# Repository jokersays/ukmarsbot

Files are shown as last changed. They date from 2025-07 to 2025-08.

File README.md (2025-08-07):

# update CW2025
## wall sensor
- LED (sichtbares Licht): TCLR5800 https://eu.mouser.com/ProductDetail/Vishay-Semiconductors/TLCR5800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
- Phototransistor: BPW96B https://www.mouser.de/ProductDetail/Vishay-Semiconductors/BPW96B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

## motor
- N20 Gear Motor mit Encoder, 6V, 20:1 / ~1000 RPM (oder 750 RPM) AliExpress?

## capacitor
- 470uF 10V 6.3mm, <12mm h, radial 2.5
- 330uF 10V radial 2.5
--> mouser

# ukmarsbot

__A simple beginner's multi purpose robot platform__

Using inexpensive, readily available materials, components and techniques, the UK Micromouse and Robotics Society (UKMARS) has created a basic robot design that can be used in a variety of common contests such as line following, wall following, drag race and mini-sumo.

UKMARSBOT V1.0 with basic wall sensor

## Contents

This repository is all about the robot itself. Software is provided in other UKMARS repositories. 

 - Software examples https://github.com/ukmars/ukmarsbot-examples
 - Full maze solving software: https://github.com/ukmars/ukmarsbot-mazerunner

The repository has a number of sections:

 - [__docs__](docs) contains miscellaneous documentation and datasheets. In there are some notes about design decisions and constraints, processor choice and configuration, and a bit about sensors.
 - [__ecad__](ecad) contains the design files for the various electronic modules that make up the robot. The original development was done with Eagle Version 7 since it was the last 'free' version of Eagle. More recent versions are likely to be developed in KiCad since it is free, unconstrained and multiplatform. You are only likely to need to look in here f you want to modify existing modules or create your own. Either Eagle or KiCad can be used for new development.
 - [__hardware__](hardware) holds subsections for the major parts that make up the robot - the main PCB and all the sensor boards. This is where you find the outputs from the ECAD tools. You don't need to know anything about Eagle or KiCad to use these outputs. For each module you should find a set of gerbers in a zip file so that you can easily order boards from your favourite supplier. Also present should be the schematics in PDF form, images of the finished boards and a parts list (BOM) to help you populate the board and select components. Note that many component choices are up to the builder and there are a number of options possible. Some or all of these elements may be missing or incomplete. Let us know of any shortcomings by raising [a new issue on github](https://github.com/ukmars/ukmarsbot/issues).
 - [__mechanical__](mechanical) contains a number of mechanical CAD files. These are most likely to be STL or STEP files  and are for components that can be 3D printed tohelp you make your robot. For example you will find motor mounts and brackets here.
 - [__renders__](renders) is a place where we keep generated images of the robot and some components. You can get an idea of how your finished robot may look as well as see some of the prototypes that led to the current design.
 - [__resources__](resources) is really a dump for stuff that does not fit in with the rest. At the tie of writing this is just a section about data logging.

## The Processor
Processor power is provided by the Arduino Nano board because it is very cheap and widely available. There is a huge range of sample code available for almost any purpose and support is easily found online. The Arduino software can be installed on any computer and is free.

A proposed pin usage for an Arduino Nano controller can be found in the [docs](docs) folder.

because the Arduino Nano is a popular processor module, there are many compatible or near-compatible alternative boards available. The processor module socket makes it possible to use some of these directly with only small modifications or, with a little more work you might fit almost any processor. Variants have already been built with STM32 processors and even a Raspberry Pi pico and Zero board.

## Bluetooth

Some alternative processors in the Arduino range already have Bluetooth and WiFi built in. If you stick with simpler options - like the Arduino Nano - there is a connector provided for you to attach one of the common HC05 or HC06 Bluetooth modules directly to the board to make a wireless serial connection. Circuitry on the board (V1.1 and later) allowyou to leave the BT module connected during programming. You can then use any serial terminal, including the Arduino terminal, to communicate with the robot over Bluetooth.

### Coding
The easiest language for starting coding with the Arduino, and the method most people use, is to create a  "Sketch" using the Arduino Integrated Development Environment (IDE). A "Sketch" comprises functions written with C/C++ statements and the Arduino IDE takes care of turning the sketch into a complete program and uploading it to the Arduino board. It can run on any of the major platforms: Windows, Mac and Linux enabling Sketch programs for the Arduino to be readily developed on any PC. The Arduino project has lots of examples and help available for creating code, as well as libraries of functions to carry out specific tasks.

The Arduino IDE requires software to be downloaded and installed on the development PC as well as drivers to enable the developed code to be downloaded using the USB cable onto the Arduino board. All of this software and drivers are free and easy to install as long as you have software install permissions on the PC.

There is also a recently introduced web based development environment, but as yet this does not support all Arduino models and platforms. and still requires various plug ins to be installed on the development PC to use it. Find out more here: https://www.arduino.cc/en/software

A very popular alternative to the Arduino IDE is PlatformIO which can be fully integrated into the excellent VSCode editor. A 'getting started' guide for this environment is available here: https://docs.platformio.org/en/latest/integration/ide/vscode.html

Alternative software environments are available and are identified at the end of this document.

### Hardware

The robot hardware is constrained by the various contest events to be within certain dimensional limits. That means that the basic chassis will be smaller than 100mm x 100mm although add-on sensors for individual events will increase the size. The robot is designed to be multipurpose so there is a core hardware setup that provides for a basic wheelchair drive of two motors, encoder feedback for individual motor speed and a minimal interface for user interaction. Components will be modular so that substitutions are easy and to provide the greatest flexibility. Builders are free to make whatever modifications suit their purpose. For example, larger or smaller motors and wheels may be used and a variety of sensor options are possible.

### Power Supply

For most purposes, the power supply for the robot will need to be compact, readily available and easy to recharge. Non rechargeable batteries are not economically viable for robot experiment and are, in any case, less environmentally friendly. Safety is a concern and so Lithium Polymer cells are only recommended when part of a regulated and protected pack. Perhaps the most common small battery is the rechargeable PP3 sized pack running at 8.4 Volts or 9 Volts. Rechargeable cells and their chargers can be purchased at supermarkets and online suppliers. More confident, or adventurous builders may install whatever power supply suits them.

### Motors

While there is endless variety in small DC electric motors, the N20-based gearmotors are excellent value for money and can be purchased in a huge range of performance characteristics. An example can be found here: [Pimoroni 20:1 gearmotor](https://shop.pimoroni.com/products/micro-metal-gearmotor-extended-back-shaft?variant=32587847050). The common dimensions make it easy to swap motors without changing the mechanical design of the robot. Versions are available with built-in encoders allowing for more accurate control of speed and greater precision in movement of the robot. Normally these would be used in any robot. The drivers for these motors are available on small circuit board modules that can easily be connected with the Arduino Nano.

### Materials

It will be possible to build the robot using parts that are commercially readily available and specialist materials will not be required. Access to basic hand tools and soldering equipment will be necessary.

It is likely that some builders will have some access to a 3D printer or a laser cutter or both and the open design of the robot with upgrade paths will allow advanced builders to utilize these tools to create higher performing robots.

### Software

The two software repositories mentioned above provide a fairly complete set of examples and code for almost every aspect of programming for the UKMARSBOT platform. Many of the techniques and examples will also be directly applicable to other mobile robot projects.

If the Arduino IDE is not for you, then there are other programming choices to suit you. (__None of these have been tried by UKMARS__)

* FlashForth http://flashforth.com/ is a Forth stamp system implemented on the Microchip 8-bit PIC18F and 16-bit PIC24, 30, 33 and the Atmel Atmega microcontroller families. See also https://playground.arduino.cc/CommonTopics/ForthOnArduino/ for other options relating to Forth.

* For Basic users there appear to be fewer options. One of these is Great Cow basic http://gcbasic.sourceforge.net/Typesetter/index.php/Home. _"The  Great Cow BASIC suite is robust and fully functional compiler and assembler.   Using Great Cow BASIC is the fastest method to program a Microchip PIC or Atmel AVR 8-bit microcontroller for those just starting and the professional user."_  The host software is cross platform and there is a graphical editor as well as a more traditional IDE.

* Some users may prefer a visual programming environment similar to Scratch. Several of these are available and more information may be found here [Sparkfun Alternative Arduino Interfaces](https://learn.sparkfun.com/tutorials/alternative-arduino-interfaces/all).

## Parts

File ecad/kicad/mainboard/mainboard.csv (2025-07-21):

'Reference' | 'Value' | 'Footprint' | 'Datasheet' | 'Qty' | 'DNP' | 'Exclude from BOM' | 'Exclude from Board'
'C1' | '100n' | 'ukmarsbot:C_Rect_L4.6mm_W2.0mm_P2.50mm_MKS02_FKP02' | '~' | '1' | '' | '' | ''
'C2,C3' | '330uF, 16V' | 'Capacitor_THT:CP_Radial_D8.0mm_P2.50mm' | '~' | '2' | '' | '' | ''
'D1' | '1N5401' | 'Diode_THT:D_DO-201AD_P15.24mm_Horizontal' | '~' | '1' | '' | '' | ''
'D3' | '1N4148' | 'Diode_THT:D_DO-35_SOD27_P7.62mm_Horizontal' | 'https://assets.nexperia.com/documents/data-sheet/1N4148_1N4448.pdf' | '1' | '' | '' | ''
'H1,H2,H3,H4,H5,H6' | 'MountingHole' | 'ukmarsbot:MountingHole_3.2mm_M3_clearance' | '~' | '6' | '' | '' | ''
'IC1' | '74HC86' | 'Package_DIP:DIP-14_W7.62mm_LongPads' | 'http://www.ti.com/lit/gpn/sn74HC86' | '1' | '' | '' | ''
'J1' | 'SENSORS' | 'ukmarsbot:1X14_LOCK_LONGPADS' | '' | '1' | '' | '' | ''
'J2,J3' | 'CONN_06SILK_FEMALE_PTH' | 'ukmarsbot:1X06_LOCK_LONGPADS' | '' | '2' | '' | '' | ''
'J4' | 'POWER' | 'Connector_Molex:Molex_KK-254_AE-6410-02A_1x02_P2.54mm_Vertical' | '~' | '1' | '' | '' | ''
'J5' | 'SERIAL' | 'ukmarsbot:1X04_LOCK_LONGPADS' | '' | '1' | '' | '' | ''
'M1' | 'Left Motor' | 'ukmarsbot:MINI-METAL-GEARMOTOR-WITH-BRACKET' | '~' | '1' | '' | '' | ''
'M2' | 'Right Motor' | 'ukmarsbot:MINI-METAL-GEARMOTOR-WITH-BRACKET' | '~' | '1' | '' | '' | ''
'R1,R2,R10' | '10k' | 'ukmarsbot:R_Axial_DIN0207_L6.3mm_D2.5mm_P7.62mm_BIGPAD' | '~' | '3' | '' | '' | ''
'R3,R11' | '4k7' | 'ukmarsbot:R_Axial_DIN0207_L6.3mm_D2.5mm_P7.62mm_BIGPAD' | '~' | '2' | '' | '' | ''
'R4' | '2k2' | 'ukmarsbot:R_Axial_DIN0207_L6.3mm_D2.5mm_P7.62mm_BIGPAD' | '~' | '1' | '' | '' | ''
'R5' | '1k0' | 'ukmarsbot:R_Axial_DIN0207_L6.3mm_D2.5mm_P7.62mm_BIGPAD' | '~' | '1' | '' | '' | ''
'R6' | '470' | 'ukmarsbot:R_Axial_DIN0207_L6.3mm_D2.5mm_P7.62mm_BIGPAD' | '~' | '1' | '' | '' | ''
'R7,R8' | '15k' | 'ukmarsbot:R_Axial_DIN0207_L6.3mm_D2.5mm_P7.62mm_BIGPAD' | '~' | '2' | '' | '' | ''
'S1' | 'sub-miniature, SPDT' | 'ukmarsbot:SW_MINI-SPDT-RTECH-78-0564' | 'https://static.rapidonline.com/pdf/560602t_v1.pdf' | '1' | '' | '' | ''
'S2' | 'BUTTON' | 'ukmarsbot:TACTILE_SWITCH_PTH_6.0MM' | '' | '1' | '' | '' | ''
'S3' | 'DIP-SW' | 'ukmarsbot:SW_DIP_SPSTx04_Slide_6.7x11.72mm_W7.62mm_P2.54mm_LowProfile' | '' | '1' | '' | '' | ''
'U1' | 'Arduino_Nano' | 'ukmarsbot:Arduino_Nano' | 'https://store.arduino.cc/usa/arduino-nano' | '1' | '' | '' | ''
'U2' | 'TB6612FNG-Module' | 'ukmarsbot:TB6612FNG-module' | 'https://cdn.shopify.com/s/files/1/0174/1800/files/TB6612FNG_3e2152f9-ac47-436b-bb2d-0abf1ce342e0.pdf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' | '1' | '' | '' | ''

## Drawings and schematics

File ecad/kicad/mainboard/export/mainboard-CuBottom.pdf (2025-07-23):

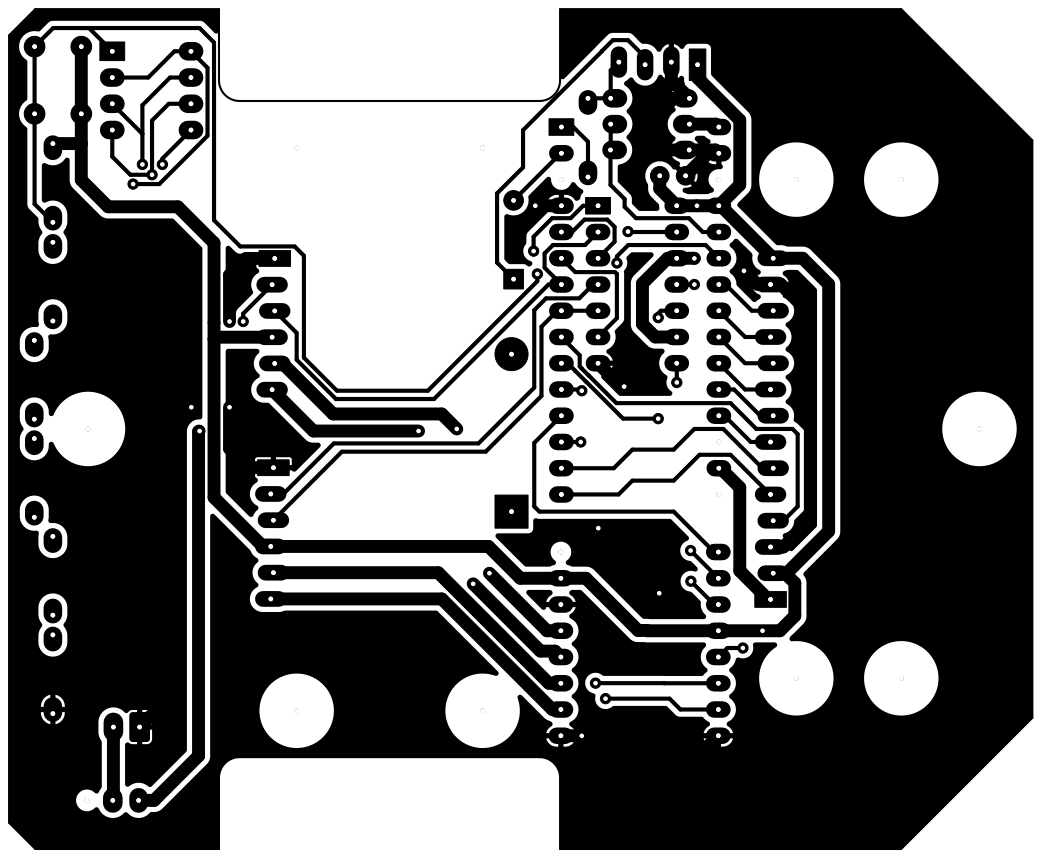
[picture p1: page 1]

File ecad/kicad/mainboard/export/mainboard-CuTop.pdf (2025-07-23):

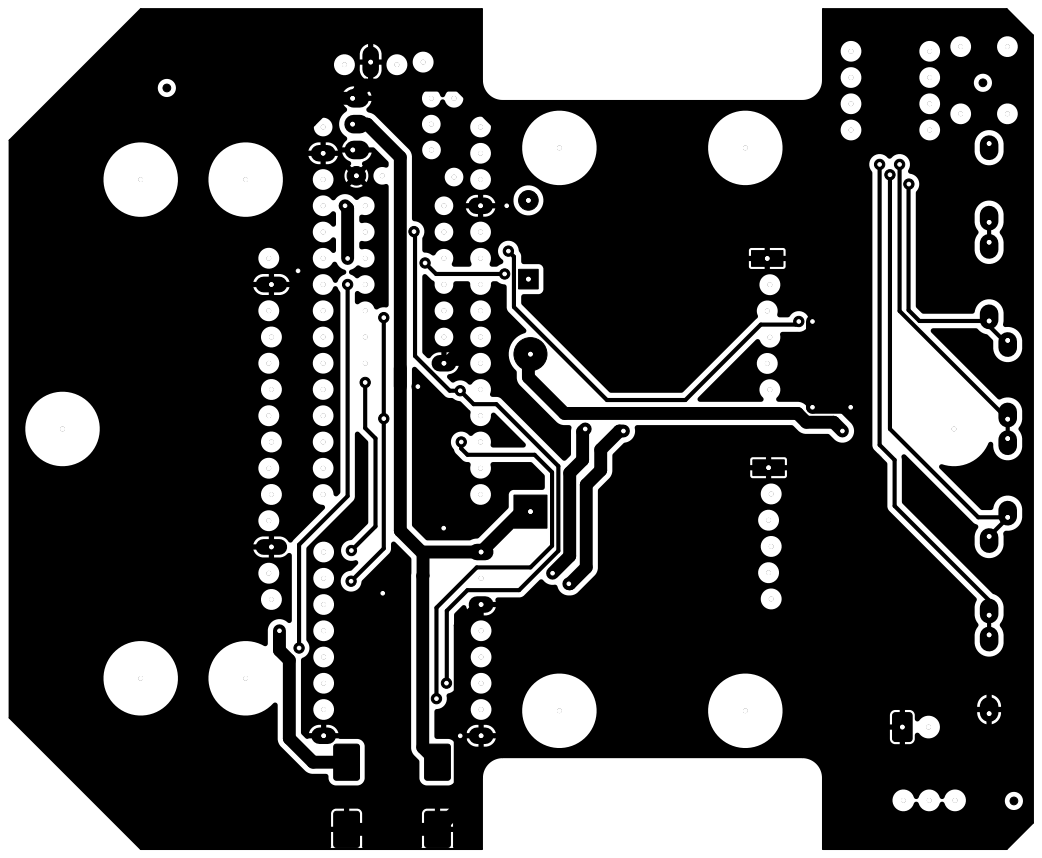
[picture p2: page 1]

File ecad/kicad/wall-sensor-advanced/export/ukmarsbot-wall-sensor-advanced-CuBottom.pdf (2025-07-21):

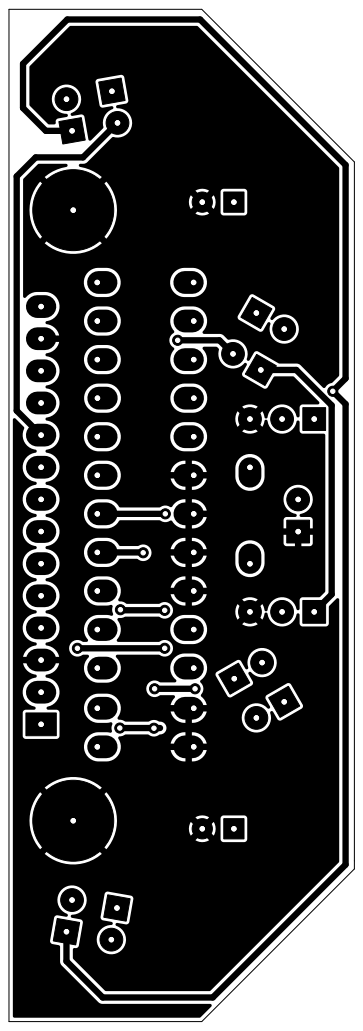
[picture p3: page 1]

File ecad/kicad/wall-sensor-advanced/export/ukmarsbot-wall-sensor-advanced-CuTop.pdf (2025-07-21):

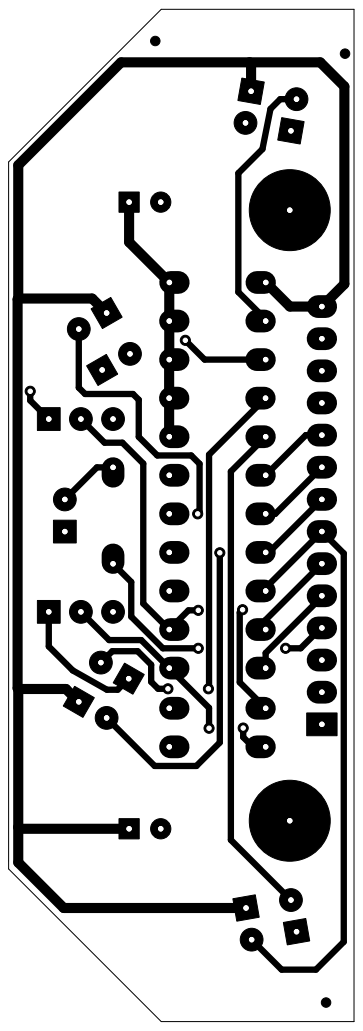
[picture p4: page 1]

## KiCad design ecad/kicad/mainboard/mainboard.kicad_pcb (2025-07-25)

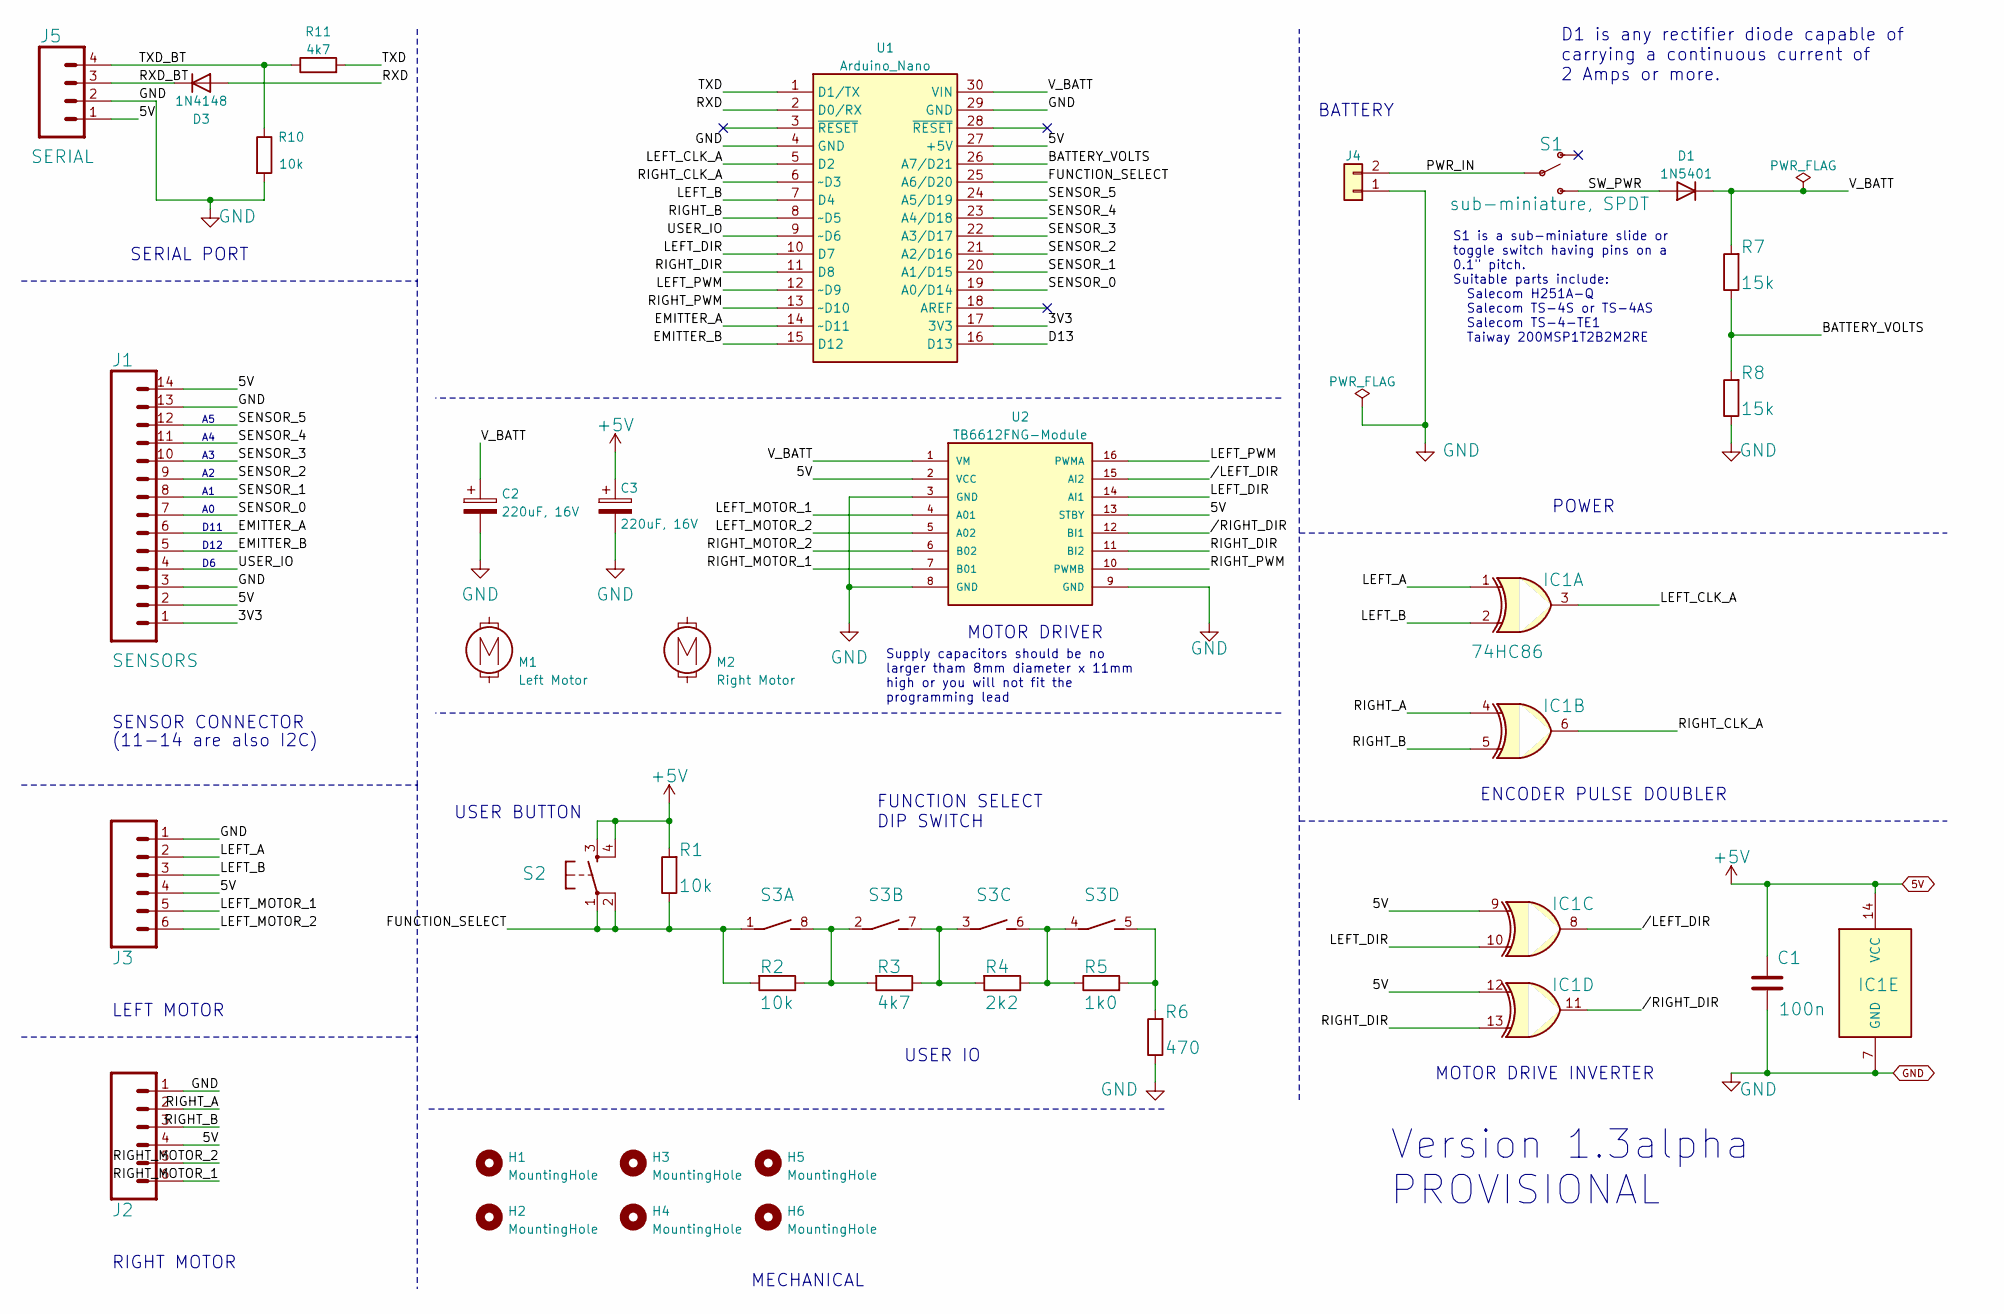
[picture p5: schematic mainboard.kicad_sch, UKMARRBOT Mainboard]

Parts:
C1: 100n; C_Rect_L4.6mm_W2.0mm_P2.50mm_MKS02_FKP02
C2, C3: 220uF, 16V; CP_Elec_8x10
D1: 1N5401; D_DO-201AD_P15.24mm_Horizontal
D3: 1N4148; D_DO-35_SOD27_P7.62mm_Horizontal
H1, H2, H3, H4, H5, H6: MountingHole; MountingHole_3.2mm_M3_clearance
IC1: 74HC86; DIP-14_W7.62mm_LongPads
J1: SENSORS; 1X14_LOCK_LONGPADS
J2, J3: CONN_06SILK_FEMALE_PTH; 1X06_LOCK_LONGPADS
J4: POWER; Molex_KK-254_AE-6410-02A_1x02_P2.54mm_Vertical
J5: SERIAL; 1X04_LOCK_LONGPADS
M1: Left Motor; MINI-METAL-GEARMOTOR-WITH-BRACKET
M2: Right Motor; MINI-METAL-GEARMOTOR-WITH-BRACKET
R1, R2, R10: 10k; R_Axial_DIN0207_L6.3mm_D2.5mm_P7.62mm_BIGPAD
R3, R11: 4k7; R_Axial_DIN0207_L6.3mm_D2.5mm_P7.62mm_BIGPAD
R4: 2k2; R_Axial_DIN0207_L6.3mm_D2.5mm_P7.62mm_BIGPAD
R5: 1k0; R_Axial_DIN0207_L6.3mm_D2.5mm_P7.62mm_BIGPAD
R6: 470; R_Axial_DIN0207_L6.3mm_D2.5mm_P7.62mm_BIGPAD
R7, R8: 15k; R_Axial_DIN0207_L6.3mm_D2.5mm_P7.62mm_BIGPAD
S1: sub-miniature, SPDT; SW_MINI-SPDT-SW
S2: BUTTON; TACTILE_SWITCH_PTH_6.0MM
S3: DIP-SW; SW_DIP_SPSTx04_Slide_6.7x11.72mm_W7.62mm_P2.54mm_LowProfile
U1: Arduino_Nano
U2: TB6612FNG-Module; TB6612FNG-module; PARTREV 11-13-17

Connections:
5V: C1.1, C3.1, IC1.9, IC1.12, IC1.14 (VCC), J1.2, J1.14, J2.4, J3.4, J5.1, R1.2, S2.3, S2.4, U1.27 (+5V), U2.2 (VCC), U2.13 (STBY)
/3V3: J1.1, U1.17 (3V3)
/BATTERY_VOLTS: R7.1, R8.2, U1.26 (A7/D21)
/D13: U1.16 (D13)
/EMITTER_A: J1.6, U1.14 (~D11)
/EMITTER_B: J1.5, U1.15 (D12)
/FUNCTION_SELECT: R1.1, R2.2, S2.1, S2.2, S3.1, U1.25 (A6/D20)
/LEFT_A: IC1.1, J3.2
/LEFT_B: IC1.2, J3.3, U1.7 (D4)
/LEFT_CLK_A: IC1.3, U1.5 (D2)
/LEFT_DIR: IC1.10, U1.10 (D7), U2.14 (AI1)
/LEFT_MOTOR_1: J3.5, U2.4 (A01)
/LEFT_MOTOR_2: J3.6, U2.5 (A02)
/LEFT_PWM: U1.12 (~D9), U2.16 (PWMA)
/PWR_IN: J4.2, S1.2
/RIGHT_A: IC1.4, J2.2
/RIGHT_B: IC1.5, J2.3, U1.8 (~D5)
/RIGHT_CLK_A: IC1.6, U1.6 (~D3)
/RIGHT_DIR: IC1.13, U1.11 (D8), U2.11 (BI2)
/RIGHT_MOTOR_1: J2.6, U2.7 (B01)
/RIGHT_MOTOR_2: J2.5, U2.6 (B02)
/RIGHT_PWM: U1.13 (~D10), U2.10 (PWMB)
/RXD: D3.2 (A), U1.2 (D0/RX)
/RXD_BT: D3.1 (K), J5.3
/SENSOR_0: J1.7, U1.19 (A0/D14)
/SENSOR_1: J1.8, U1.20 (A1/D15)
/SENSOR_2: J1.9, U1.21 (A2/D16)
/SENSOR_3: J1.10, U1.22 (A3/D17)
/SENSOR_4: J1.11, U1.23 (A4/D18)
/SENSOR_5: J1.12, U1.24 (A5/D19)
/SW_PWR: D1.2 (A), S1.3 (S)
/TXD: R11.2, U1.1 (D1/TX)
/TXD_BT: J5.4, R10.1, R11.1
/USER_IO: J1.4, U1.9 (~D6)
/V_BATT: C2.1, D1.1 (K), R7.2, U1.30 (VIN), U2.1 (VM)
//LEFT_DIR: IC1.8, U2.15 (AI2)
//RIGHT_DIR: IC1.11, U2.12 (BI1)
GND: C1.2, C2.2, C3.2, IC1.7 (GND), J1.3, J1.13, J2.1, J3.1, J4.1, J5.2, R6.1, R8.1, R10.2, U1.4 (GND), U1.29 (GND), U2.3 (GND), U2.8 (GND), U2.9 (GND)
unnamed: R2.1, R3.2, S3.2 (1), S3.8 (2)
unnamed: R3.1, R4.2, S3.3 (1), S3.7 (2)
unnamed: R4.1, R5.1, S3.4 (1), S3.6 (2)
unnamed: R5.2, R6.2, S3.5 (2)

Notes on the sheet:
MOTOR DRIVER
D1 is any rectifier diode capable of carrying a continuous current of 2 Amps or more.
USER IO
POWER
MOTOR DRIVE INVERTER
FUNCTION SELECT DIP SWITCH
Supply capacitors should be no larger tham 8mm diameter x 11mm high or you will not fit the programming lead
S1 is a sub-miniature slide or toggle switch having pins on a 0.1" pitch. Suitable parts include: Salecom H251A-Q Salecom TS-4S or TS-4AS Salecom TS-4-TE1 Taiway 200MSP1T2B2M2RE
RIGHT MOTOR
SERIAL PORT
SENSOR CONNECTOR
BATTERY
MECHANICAL
ENCODER PULSE DOUBLER
USER BUTTON
D11
Version 1.3alpha PROVISIONAL
LEFT MOTOR
(11-14 are also I2C)
D12

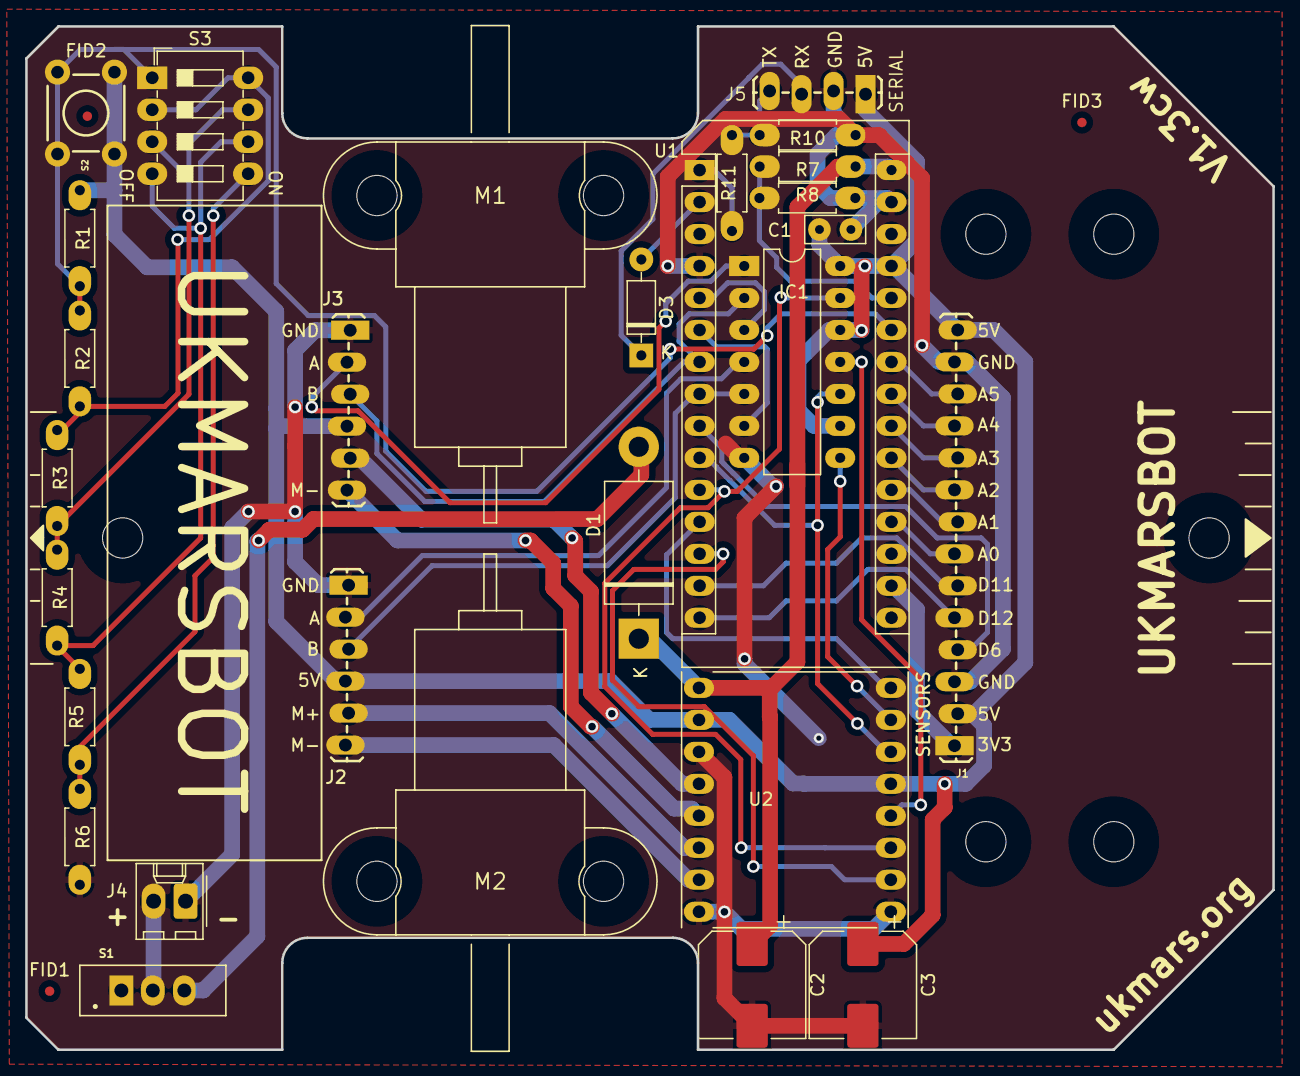
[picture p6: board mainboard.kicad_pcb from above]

Board: 2 copper layers, 99.1 x 81.3 mm, 37 parts (0 on the bottom side), 41 nets.

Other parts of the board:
FID1, FID2, FID3: Fiducial_0.75mm_Mask1.5mm

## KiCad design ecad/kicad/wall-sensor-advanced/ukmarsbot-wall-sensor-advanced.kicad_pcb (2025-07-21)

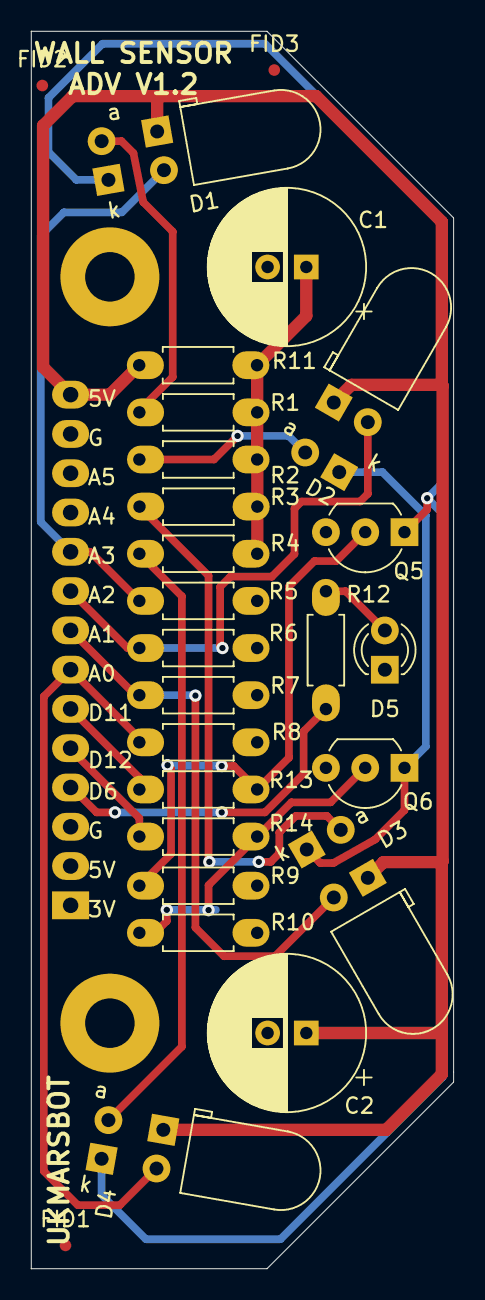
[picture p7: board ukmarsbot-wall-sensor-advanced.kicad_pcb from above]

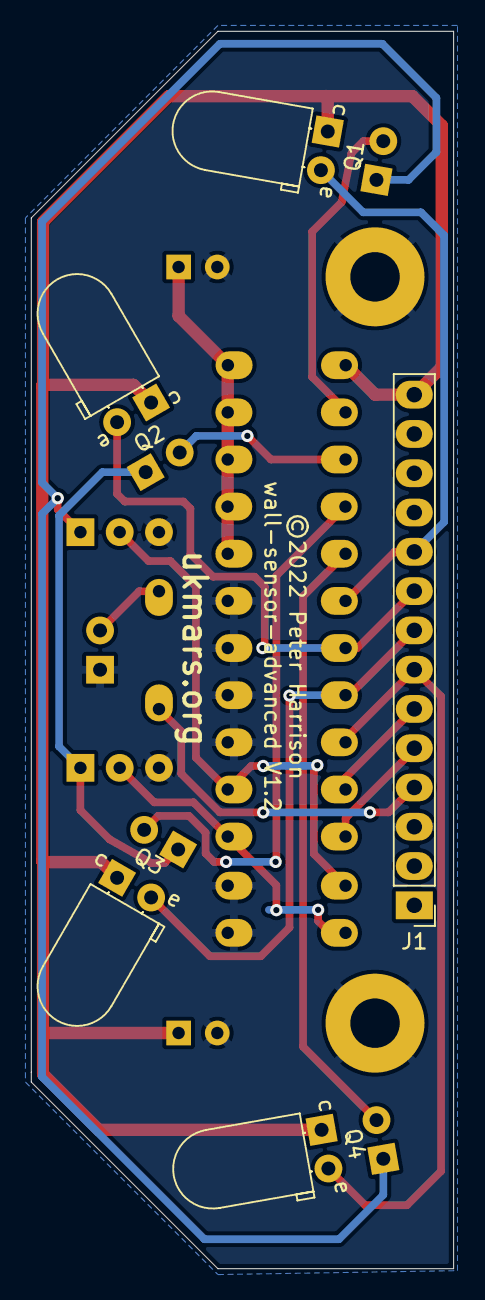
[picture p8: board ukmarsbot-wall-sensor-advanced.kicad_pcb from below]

Board: 2 copper layers, 27.3 x 80.0 mm, 33 parts (5 on the bottom side), 19 nets.

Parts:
C1, C2: 330uF, 16V; CP_Radial_D10.0mm_P2.50mm
D1, D2, D3, D4: SFH4545; LED_D5.0mm_Horizontal_O6.35mm_Z3.0mm
D5: LED; LED_D3.0mm
FID1, FID2, FID3: Fiducial_0.75mm_Mask1.5mm
H1, H2: 3.2mm; MountingHole_3.2mm_M3_Pad
J1: Conn_01x14; PinHeader_1x14_P2.54mm_Vertical_Longpads
Q1, Q2, Q3, Q4: TEFT4300; LED_D5.0mm_Horizontal_O1.27mm_Z3.0mm_IRGrey
Q5, Q6: BC337; TO-92_Inline_Wide_HandSolder
R1, R2, R3, R4: 10R; R_Axial_DIN0207_L6.3mm_D2.5mm_P7.62mm_BIGPAD
R5, R6, R7, R8: 1k8; R_Axial_DIN0207_L6.3mm_D2.5mm_P7.62mm_BIGPAD
R9, R10: 100k; R_Axial_DIN0207_L6.3mm_D2.5mm_P7.62mm_BIGPAD
R11: 33; R_Axial_DIN0207_L6.3mm_D2.5mm_P7.62mm_BIGPAD
R12: 1k0; R_Axial_DIN0207_L6.3mm_D2.5mm_P7.62mm_BIGPAD
R13, R14: 390R; R_Axial_DIN0207_L6.3mm_D2.5mm_P7.62mm_BIGPAD

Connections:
5V: C2.1, J1.14, Q1.1 (C), Q2.1 (C), Q3.1 (C), Q4.1 (C), R11.2
/DIA_COMMON: D2.1 (K), D3.1 (K), Q6.1 (C)
/FWD_COMMON: D1.1 (K), D4.1 (K), Q5.1 (C)
A0_RF: J1.7, Q4.2 (E), R8.1
A1_RD: J1.8, Q3.2 (E), R7.1
A2_LD: J1.9, Q2.2 (E), R6.1
A3_LF: J1.10, Q1.2 (E), R5.1
D6_LED: J1.4, R12.2
D11_FRONT: J1.6, R13.1
D12_DIAGONAL: J1.5, R14.1
GND: C1.2, C2.2, D5.1 (K), H1.1, H2.1, J1.3, J1.13, Q5.3 (E), Q6.3 (E), R5.2, R6.2, R7.2, R8.2, R9.2, R10.2
unnamed: D1.2 (A), R1.1
unnamed: D2.2 (A), R2.1
unnamed: D3.2 (A), R3.1
unnamed: D4.2 (A), R4.1
unnamed: D5.2 (A), R12.1
unnamed: Q5.2 (B), R9.1, R13.2
unnamed: Q6.2 (B), R10.1, R14.2
V_LED: C1.1, R1.2, R2.2, R3.2, R4.2, R11.1

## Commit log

2025-07-21 Zwischenstand: IBOM, Layout
    [mainboard-BOT.gbr, mainboard-B_Cu.gbr, mainboard-Eco1_User.gbr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]
2025-07-22 Zwischenstand Layout
    [mainboard.kicad_pcb]
2025-07-22 changed pads to connected layer only
    [mainboard.kicad_pcb]
2025-07-22 changed all pads to connected layer only
    [mainboard.kicad_pcb]
2025-07-22 Layout fertig (fast)
    [mainboard.kicad_pcb, mainboard.kicad_sch]
2025-07-23 final layout 1.3cw
    [mainboard.kicad_pcb, mainboard.kicad_sch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]
2025-07-23 ibom neu
    [mainboard-BOT.gbr, mainboard-TOP.gbr]
2025-07-25 added missing via
    [mainboard.kicad_pcb]

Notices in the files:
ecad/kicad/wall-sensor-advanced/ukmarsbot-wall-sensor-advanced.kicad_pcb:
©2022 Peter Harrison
